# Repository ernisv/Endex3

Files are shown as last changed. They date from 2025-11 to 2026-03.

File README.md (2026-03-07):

# Project "Endex3"
Ender 3 Idex conversion

Prototype:

<p align="center">
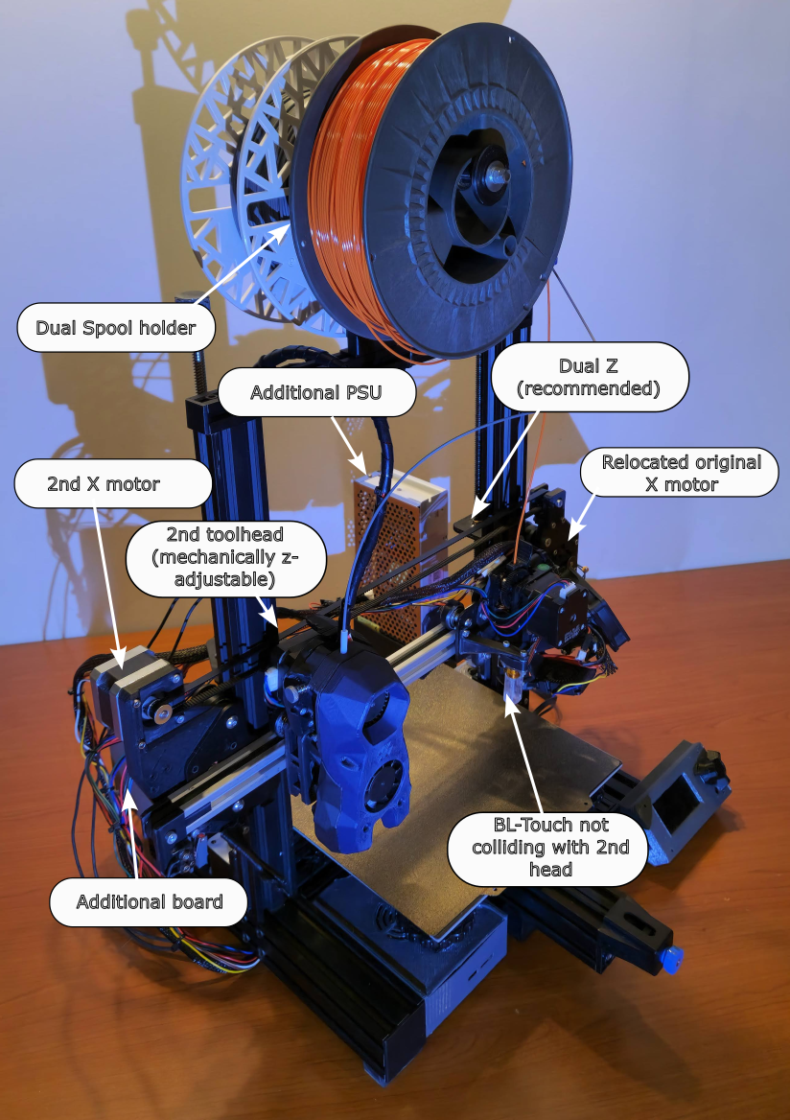
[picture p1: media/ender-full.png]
Conversion in reality

</p>

Idex in action:
[Idex in action](media/idex-in-action.mp4)

## Would like to get a support?
* Ask in platforms below
* Use Github issues
* Ask in [discord](https://discord.gg/aMRszwNQSe)

## Would like to support?
If you like the project or find it useful, you may support it here:
* https://buymeacoffee.com/ernisv
* https://patreon.com/ernisv

## Goals

* fully functional Idex
  * multimaterial printing without excessive filament/print time waste
  * copy mode
  * mirror mode
* no loss of printable area for at least one of the heads
* ooze prevention for idle nozzle
* controlled by Klipper firmware
* footprint width not to exceed 50cm
* reuse of commodity 3d printing parts of Ender3 era

## Additional hardware 

* NEMA17 stepper motor for new toolhead with wires
* GT2 6mm belt - about 90cm
* GT2 pulley for the motor
* GT2 idler
* 3 additional V-Wheels
* various M3 and M5 bolts (inner hex heads)
* M4 bolt for additional X GT2 idler
* 2 compression springs (~20nn) for M5 bolts on height adjustable toolhead mount
* microswitch for second X endstop
* 410mm 2020 extrusion for longer X gantry
* new toolhead - extruder with stepper, heating block, thermistor, hotend and part cooling fan, wires
* Klipper compatible control board to control:
  * 2 stepper motors - additional X motor, additional extruder
  * control new toolhead's heater
  * control new toolhead's part cooling fans
  * monitor new toolhead's temperature
* additional power needs  
  * can be small additional ~220W PSU that could power the heated bed
  * or complete 550W+ replacement for original PSU
  
## Conversion story
So before all that there was a Creality Ender3 V2, which was a first printer and during many years it morphed little by little to gain more speed, more flowrate, bed levelling, magnetic bed, Klipper.. and still was printing reliably enough to avoid being replaced by anothing more modern :)

But there was still a feature that it missed - multimaterial printing. And in 2025 - year when multimaterial became the norm with all multiplexing filament changers and even proper toolchangers coming, this became a matter of survival for the Ender3..

And the solution for that was one - Idex conversion. Idex is better than filament changers as produces less waste and switches materials much faster and even offers some interesting unique features that even proper toolchangers do not have - copy and mirror modes when single printer essentially is doing work for two :) 

So it started in CAD, trying to sqeeze additional axis belt, motors and toolhead while keeping bulky v-wheels system and most stock hardware.. 

After some time theoretically everything looked good in CAD.. did not work in practice though :)

First issues were random resets when bed heating and both toolheads were working simultaneously. 
In fact stock PSU now had to support 3 new stepper motors:
- dual X motor (one of previous mods), new extruder motor and new X motor,
- additional hotend heater,
- additional fans.
So it was solved by getting additional 24V PSU and it taking care of powering heated bed, so that all the rest could stay on original PSU.

At this point and quite a bit of calibrations and tuning, this amazing print was produced by both toolheads collaboratively.

<p align="center">
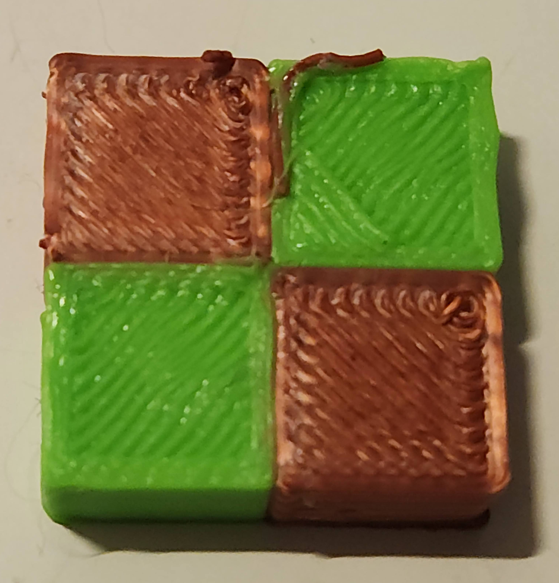
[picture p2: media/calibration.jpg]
Idex calibration done

</p>

It looked like a success.. but bigger prints still failed after some time - printheads were clogging. Especially the original Ender3 hotend. 
It was already modified previously - all metal heatbreak and Volcano nozzle for bigger flowrate, it even had bigger 60mm hotend fan in place of stock 3010 to solve the previous issues with heat creep. 
And this worked for single toolhead prints, when there was constant flow of filament being pushed through.

However now, when it needed to sit idle for minutes between extrusions - old issues came back.. so in the end to complete Idex conversion, stock hotend had to be replaced.

Checking the drawers yielded V6 hotend and direct drive Titan extruder. None of existing public designs for direct drive with hardware i had at hand did fit due to contraints of additional X belt and second toolhead, so it ment one - back to the CAD again..

And it worked out, but produced this monstrocity. This is not a suggestion to use the same for anyone wanting to do similar conversion by any means :) 

<p align="center">
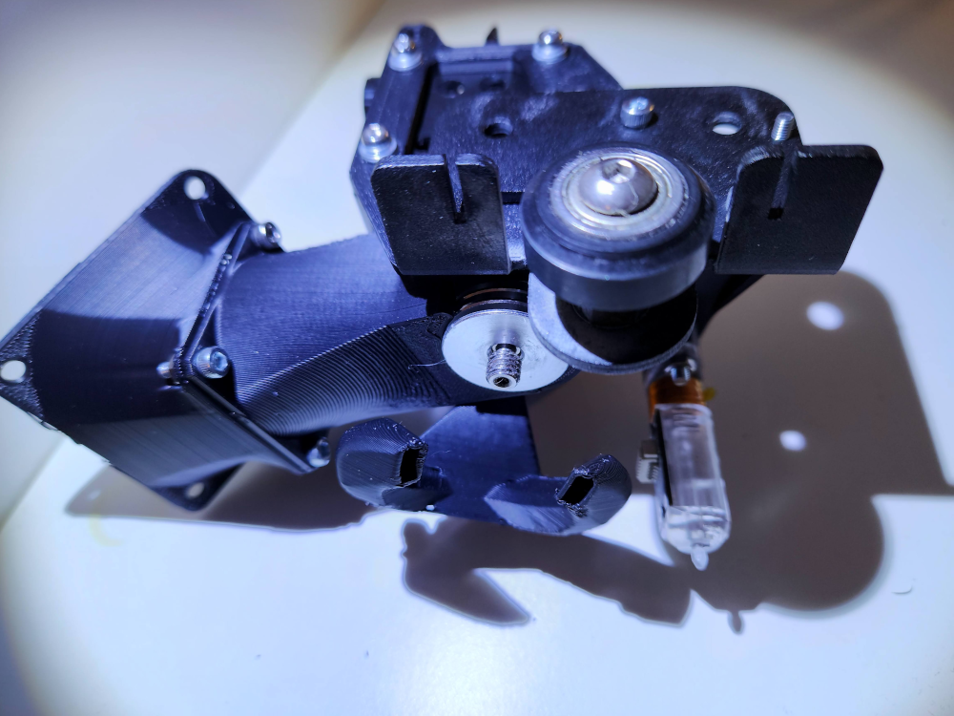
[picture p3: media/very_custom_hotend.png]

</p>

And finally it was working, evidence below !

<p align="center">
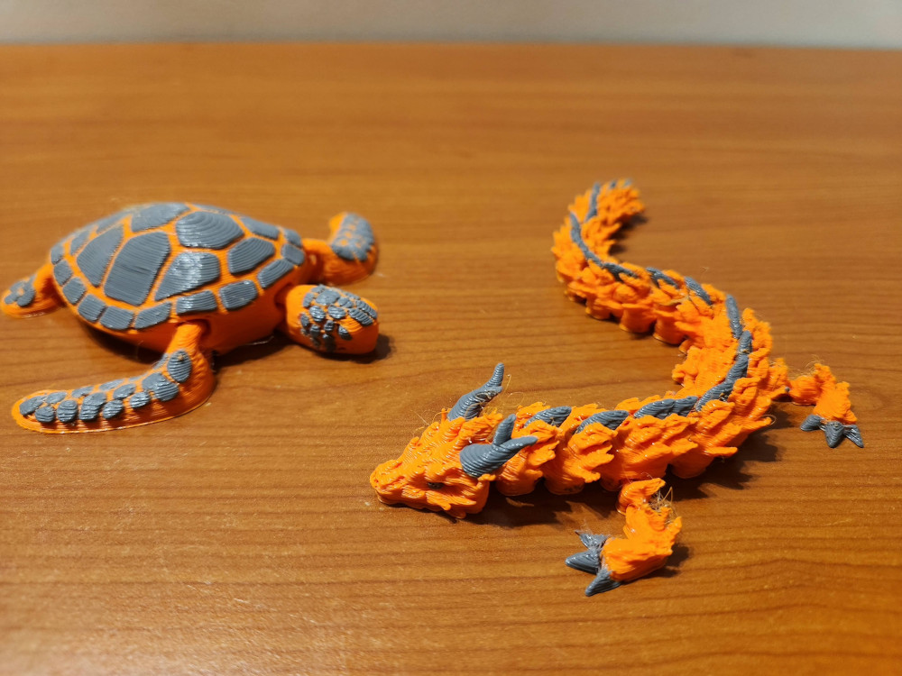
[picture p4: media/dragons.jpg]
Idex prints

</p>

What looked like a quick, relatively straightforward mod, took way more than expected - but now it's finished and working. It's shared here as there are not a lot of public designs leveraging mostly stock parts.
Also i'm sharing the same parts here:
* https://www.printables.com/@ErnestasVai_465342/models
* https://www.thingiverse.com/ernisv/designs

Now let's dive into each individual component/change to be able to create more Endexes.

Also if your drawers have different components - adaptations and variations of this conversion could be gathered here, please raise a Pull Request with suggested changes.

## Details / component changes
Changes to individual components are broken down below. If unsure about dimensions / assembly - step files and/or original [Onshape CAD](https://cad.onshape.com/documents/81a2e00ae9c5806eab5e1c54/w/5cac38db4e9fa7317548eab6/e/0372a484cd82c8e6febd21dc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) could be checked.

STLs from CAD are exported here: [STL](STL).

When "left" or "right" is mentioned, it's from perspective of looking at the printer from the front.

### X gantry
#### Longer 2020 extrusion
As stock x axis has space only for original head, putting another one on the same would significantly reduce the bed area accessible by any single head, so extension of this is necessary.
This is likely the most mechanically difficult part of the conversion as it needs replacement of stock extrusion and drilling correct holes at the same places as in old one.

The length of new 200 v-slot extrusion should be 410mm (could be reduced to around 400mm, but endstop mount will have to be mounted in some more compact way).

It is important to ensure that the left end (from perspective of looking at the printer from the front) of new extrusion is protruding 65mm from the end of original one, then original extrusion could be fixed together with the new one and used as a guide for drilling pilot holes.
To doublecheck - distance from the new extrusion left end to the first hole center should be 68mm.

<p align="center">
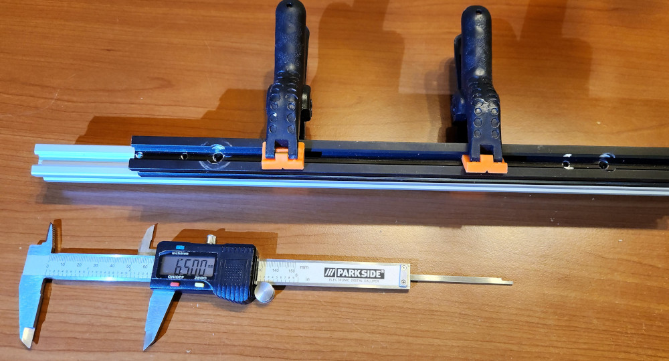
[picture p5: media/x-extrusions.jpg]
X Extrusions

</p>

*Note:* it needs to be v-slot extrusion, not t-slot, cause t-slot is not designed for v-wheels.

Once pilot holes are drilled - you will need to complete the drilling and tap the threads in M3 holes.

You will need:
* 3mm drill bit,
* 5.5mm drill bit,
* M3 tap,
* 11mm drill bit or dremel to clear space for M5 bolt heads from one side.

#### Original X belt / motor
With longer extrusion, original X motor placement is no longer an option. But moving motor further to the left would not allow to fit into 50cm width footprint.
So original X motor had to go to the right side onto newly designed mount where previously was a x belt tensioner.
Belt still goes inside the extrusion like before.

### Additional X belt
Now when original X motor was relocated to the right side, to keep weights balanced - new X motor should go to left side on new mount plate.
The required new GT2 6mm belt length is about 90cm.

#### X endstops
Left endstop is a microswitch having 2 holes for M3 with 10mm distance between them.
<p align="center">
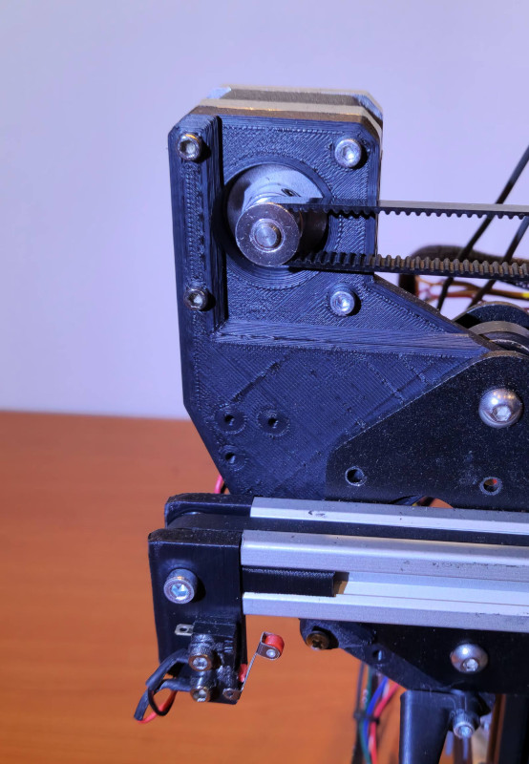
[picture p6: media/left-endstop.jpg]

</p>

Right one has a mount sliding into extrusion and bolting on original x endstop.
<p align="center">
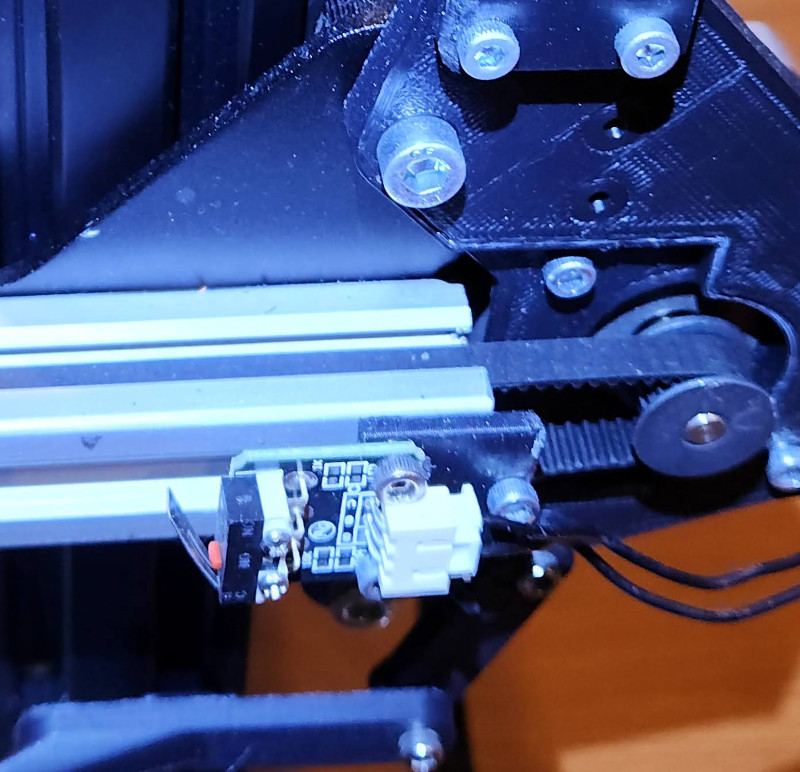
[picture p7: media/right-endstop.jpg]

</p>

#### Ooze prevention
Idling heads will ooze some filament even if slicer reduces idle temperatures - they won't drop immediately. To help with that, X gantry includes ooze blockers, that cover the nozzles when heads are in idle park positions.

They are slightly adjustable, printed in ABS and are supposed to have clamped strips of high temp silicone for the immediate contact area with the nozzles. Simplest way is to take heatblock silicone socks and cut out strips from them.

<p align="center">
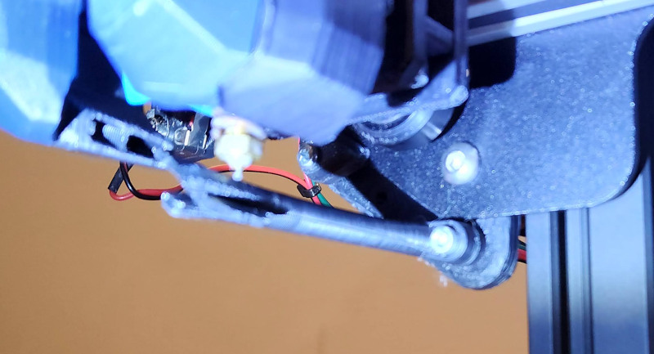
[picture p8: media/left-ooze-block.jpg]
Left ooze block

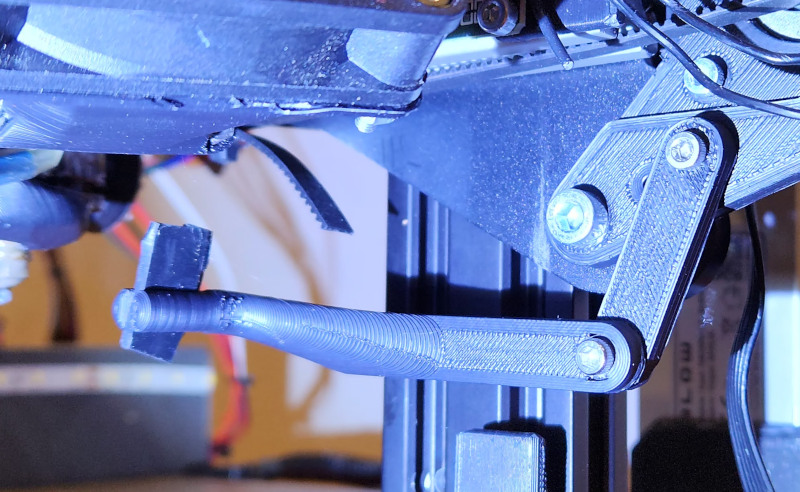
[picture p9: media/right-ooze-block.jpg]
Left ooze block

</p>

#### Dual Z
It's not strictly necessary, but highly recommended as weight of x gantry has increased.
This conversion has no particular solution included, but there are lots of publicly available options for Ender3 v2 dual Z axis.

#### Gantry levelling
With increased X gantry weight there are more possibilities for it to get out of alignment. If dual Z solution uses belt-synchronized Z sides, it may be less relevant, but still useful.

This conversion has two blocks of equal size on which X extrusion could be rested until a touch (manually, with heads out of bed area in park positions).
Right block can remain attached permanently, but left one blocks X head movement when attached, so it is a clip-on to be attached only during alignment.
<p align="center">
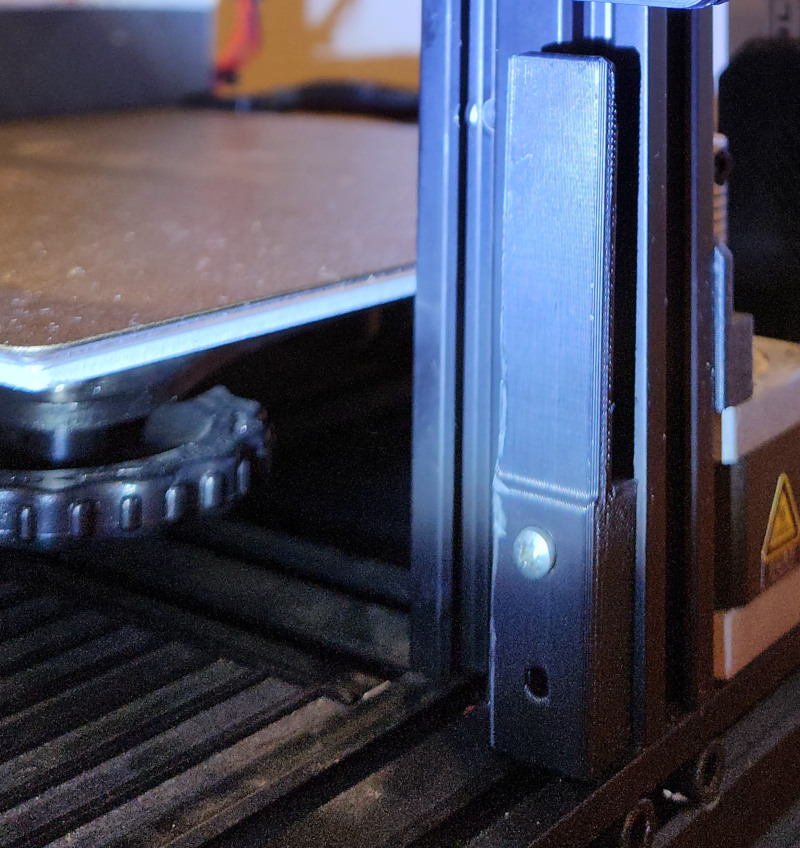
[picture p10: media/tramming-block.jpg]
Left ooze block

</p>

### 2nd toolhead
#### Stealthburner
2nd toolhead has limited access across X axis, so the narrower it is - the less limitation. 
And Voron's Stealthburner looked like a quite compact option with regard to X-footprint.

Also it's a popular toolhead with lots of mods, which helped me to use the components i had available.
I had pancake NEMA17 motor, V6 heatsink with Volcano nozzle, so i used these mods to make use of them.

* [V6+Volcano mod](https://www.printables.com/model/561529-voron-stealthburner-v6volcano-toolhead-extension-m)
* [NEMA17 pancake mod](https://www.printables.com/model/454292-voron-stealthburner-clockwork2-extruder-nema17-v1)
  * *note:* use idler from the step files, as STL has some older incompatible part (see comments)

#### Mechanical Z adjustments
Nozzles of both Idex heads should be aligned vertically in relation to each other with quite a high precision (to be at least a fractions of of a layer's hight).

While for dual-material printing maybe it could be adjusted by software z-offsets, for copy/mirror mode especially - they need to be physically aligned.
Because of that a mount with mechanically adjustable height was designed.

<p align="center">
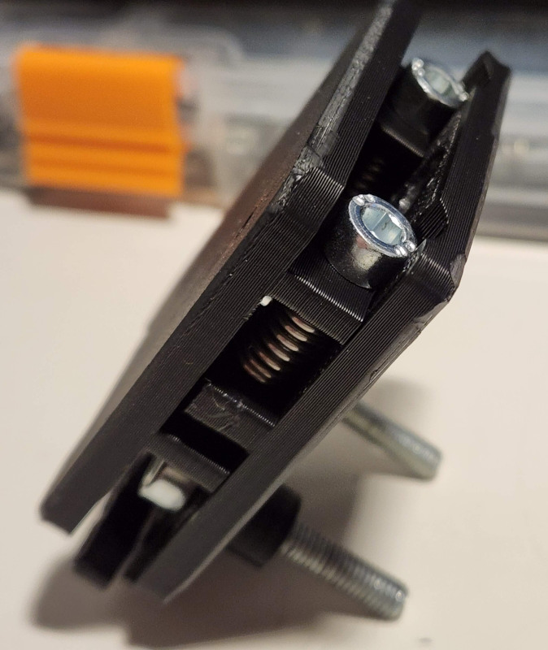
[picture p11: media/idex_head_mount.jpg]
Idex adjustable head mount

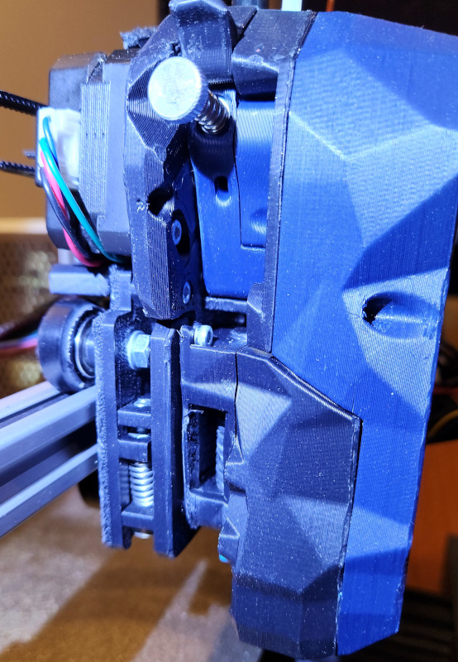
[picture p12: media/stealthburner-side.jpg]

</p>

Here some springs were used together with M5 adjustability bolts, you need to adjust both bolts equally to avoid skew.

The alignment process i used:
* home the printer, clear the heightmap
* via Klipper web UI move the original nozzle somewhere near the middlge of the bed and lower to minimal distance from bed like in "paper test" (paper sheet just lightly gripped between nozzle and bed surface)
* raise Z, change the active head to secondary
* near the same bed point carefully try to lower the nozzle to the same z position original nozzle hand
  * if paper grips earlier or later than first nozzle - raise the Z, adjust the adjustment screws and recheck 

### Original toolhead
Stock bowden toolhead should work fine with this conversion. My prototype used volcano nozzles, which are 8.5mm longer on both toolheads, but basically what's required is that both tools would have nozzles at roughly the same height, that would be within adjutability range of Idex head mount. 
So if stock head and nozzle is used - stealthburner should also use nozzle of similar height to stock nozzle, not Volcano height.

#### Bed probe
Also most likely you already use some kind of bed probe, prototype printer used Bltouch. Common probe mounts might occupy more space than necessary on the side of toolhead, which would limit how close both heads could come together. So this conversion includes Bltouch mount that moves it furter forward, but occupying less space along X axis.

<p align="center">
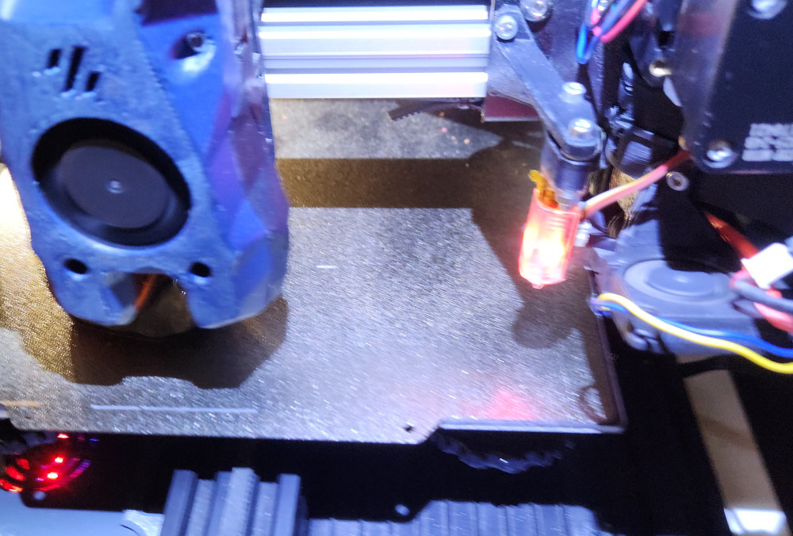
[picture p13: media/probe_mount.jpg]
Bed probe mount

</p>

#### Suitable alternatives
Prototype needed some custom adjustments, because it used direct drive conversion with full size NEMA17 motor and most direct drive mods with such motor did not clear space above the X extrusion to clear the belts and allow additional travel to the right. 

But that does not mean there wouldn't be suitable direct drive mods with more compact components that are compatible.

So what needs to be considered when choosing direct drive mod:
* clearance for the additional belts above X extrusion,
* clearance of additional travel to the right - it should not hit Y extrusion,
* distance from the left of the head - isn't it limiting how close both heads could come together,
* the endstop from the right.

### Second control board
Prototype printer had already replaced stock board to SKR Mini E3, however as this and most usual replacement boards would not support additional 2 stepper motors, heater, thermistor and fan - second board would be needed.
I used stock Ender3 board for that.

In general you just need to connect and setup 2 boards to the device running Klipper (usually SBC like Raspberry Pi or regular linux PC).

### Additional PSU
As it turns out stock PSU capacity might be not enough to power all additional hardware - it either needs to be replaced by more powerful one - 550W should be enough.

Or as a more budget option - add a smaller additional PSU to just power the heated bed, which would take quite a big portion of load from original PSU.
Moreover there is a place to mount PSU like original Ender3's did - on the right/back.

Mounting options are also plenty, it depends on exact PSU you have. The mount included in conversion is for "Blow 24V PSU" i've got (still running.. still not blown!).

The stock Ender3v2 bed should take around 220W.

Klipper's config setting `max_power` could also be used to try limiting power consumption.

How i connected additional PSU to work only as dedicated PSU for heated bed:
* New PSU ground / earth <--> Old PSU ground / earth
* New PSU -24V <--> Old PSU -24V
* New PSU +24V <--> Bed +
* Board Bed - <--> Bed -
* Board Bed + <--> *Unconnected!*

This is done so, because MOSFET on the board controls connection to the -, while Bed+ provides constant +24V from PSU.

<p align="center">
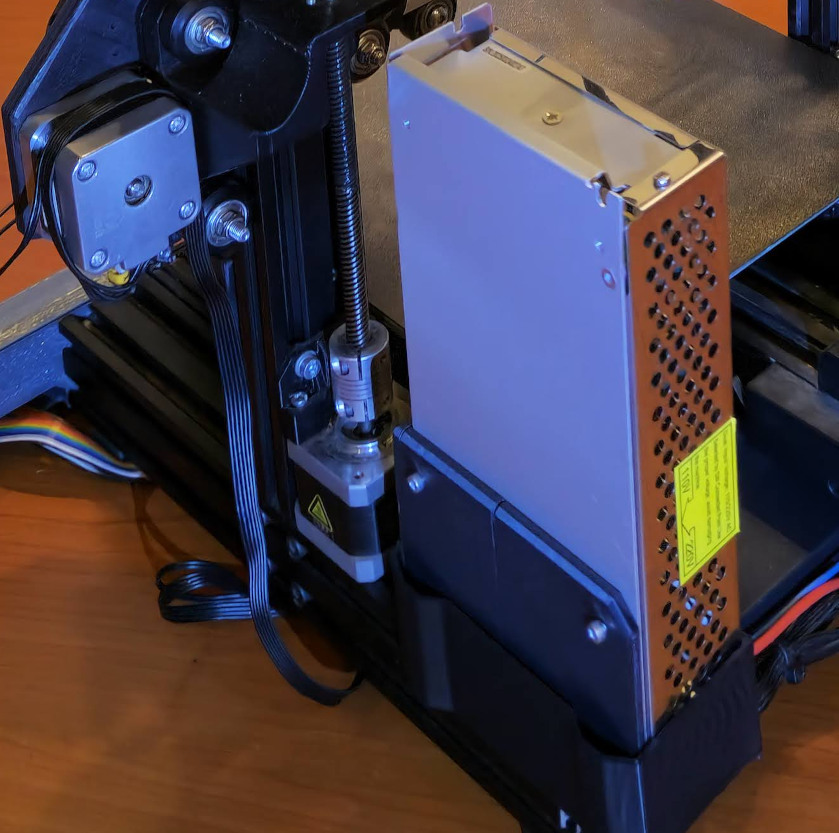
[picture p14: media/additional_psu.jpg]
Additional PSU

</p>

### Klipper configs

[Klipper configs](KlipperConfigs) directory contains example of Klipper config files used in the prototype. 
It won't be drop-in config, but rather an example to base on, so that assumes basic Klipper knowledge.

### Printing the parts
I tried to design parts to not require supports, so most parts can be printed without them.
Although i printed all the parts in ABS - i did so because that printer is usually printing in an enclosure, where it could get pretty hot.
But if it's not the case - ABS would only be recommended for parts closer to hotends, like fan ducts, heatsink mounts, also ooze blocks.
Other parts should work fine printed with PETG/PLA. 

## Contributing mods / improvements
If you make an improvement or adaptation - let others know by raising a PR! 
We'll merge it into this repository and maybe this could become a modular and flexible project.

If it's not a change to existing parts, but alternative/adaptation, it could go to separate directory with small individual description, then we could create easily searchable list of mods.

List of improvements currently needing work can be found in [TODO.txt](TODO.txt).

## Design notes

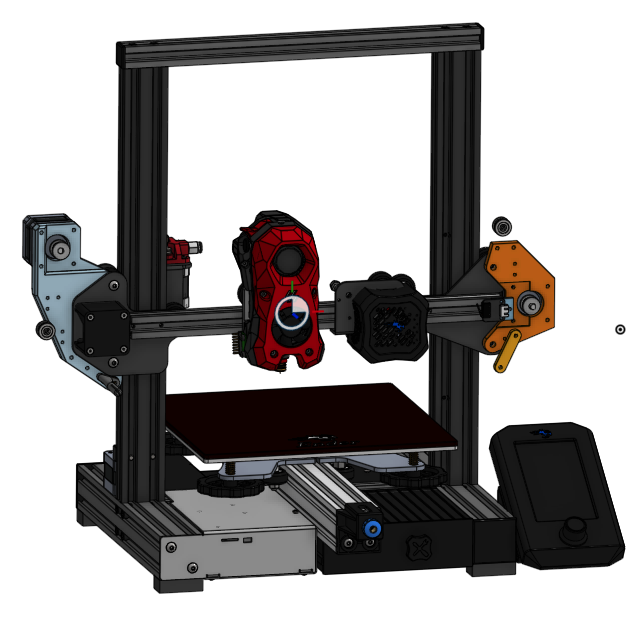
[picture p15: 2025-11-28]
media/ender-cad.png

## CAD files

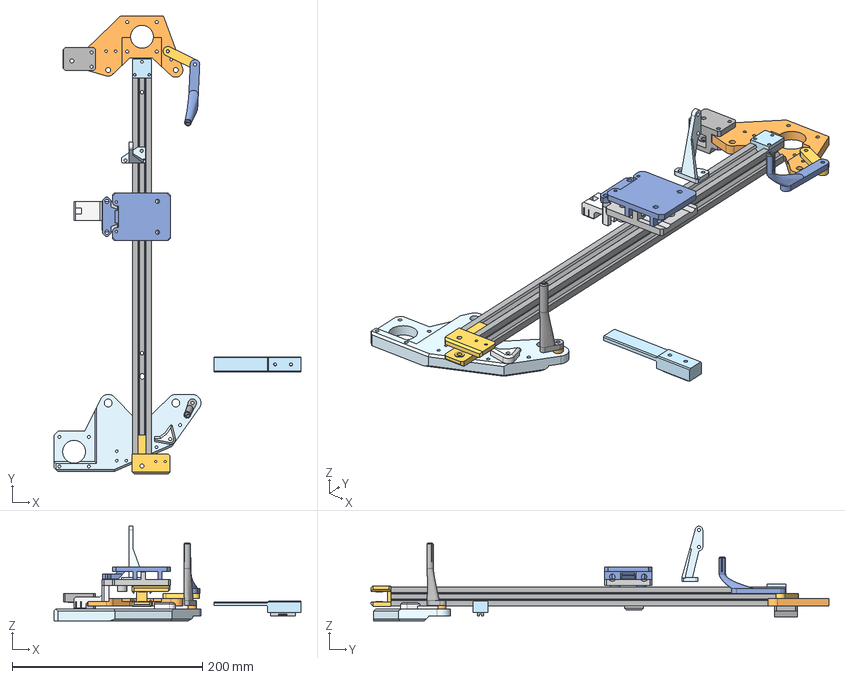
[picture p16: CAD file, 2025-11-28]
STEP/XGantry.step
259.5 x 481.3 x 99.5 mm

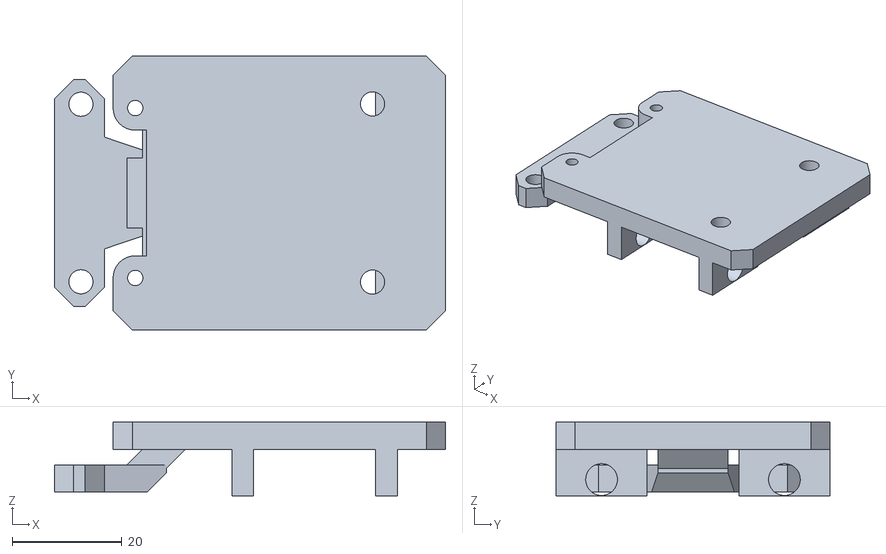
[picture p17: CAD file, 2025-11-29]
STL/XGantry - StealthburnerBracket.stl
71.3 x 50.0 x 13.5

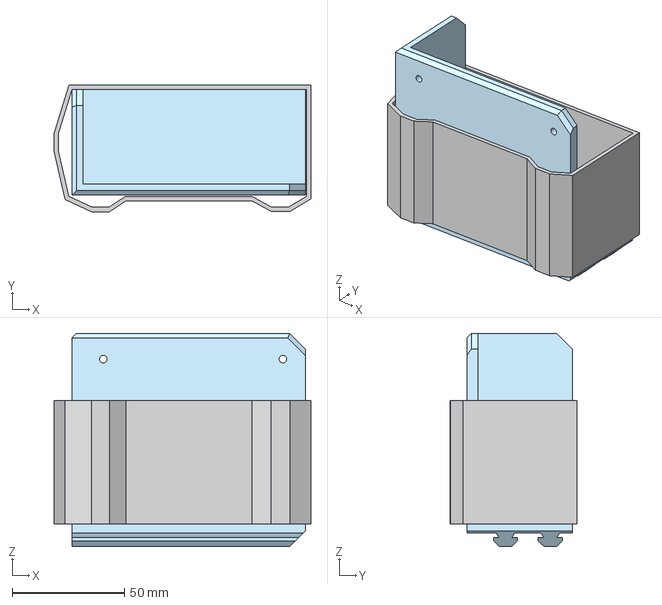
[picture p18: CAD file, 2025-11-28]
STEP/Misc Parts - PSU Mount.step
114.5 x 56.4 x 95.0 mm

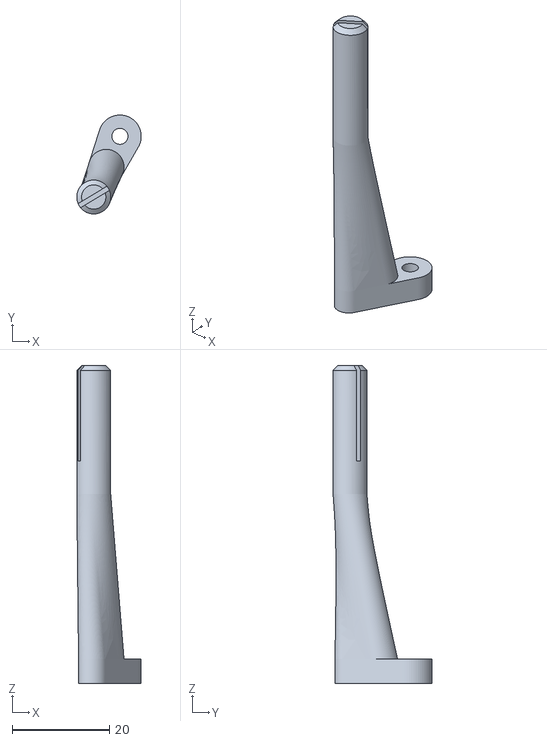
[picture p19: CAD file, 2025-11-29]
STL/XGantry - LeftOozeBlock.stl
13.3 x 20.4 x 65.5

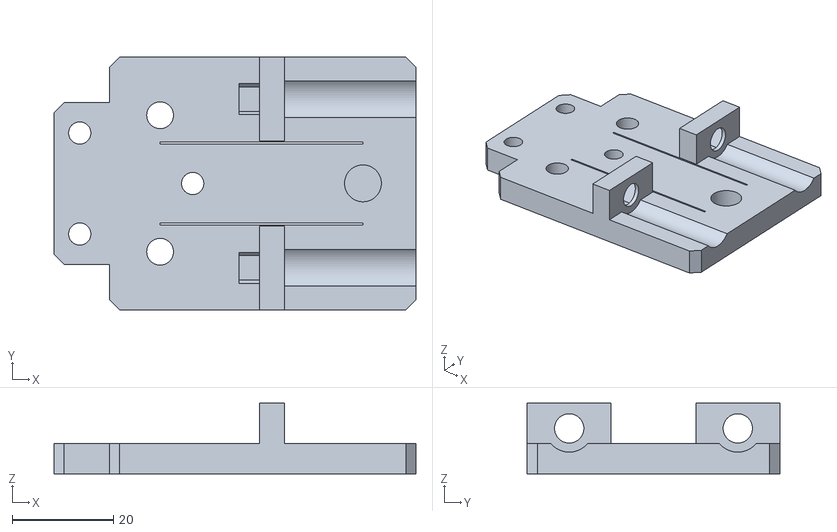
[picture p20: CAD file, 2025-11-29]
STL/XGantry - StealthburnerCarriage.stl
71.6 x 50.0 x 14.0

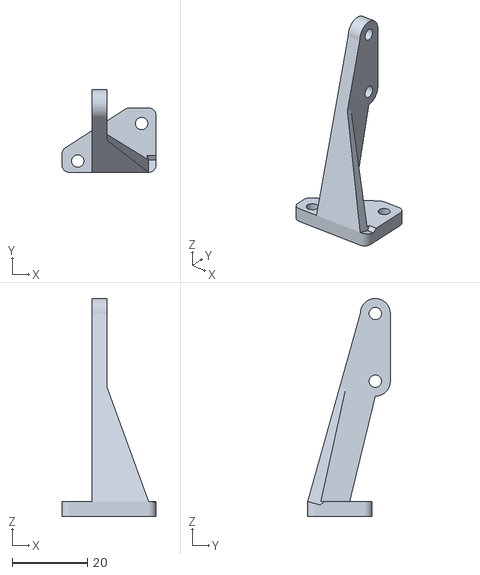
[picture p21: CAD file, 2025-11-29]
STL/XGantry - BLTouchMount.stl
25.1 x 22.0 x 58.0

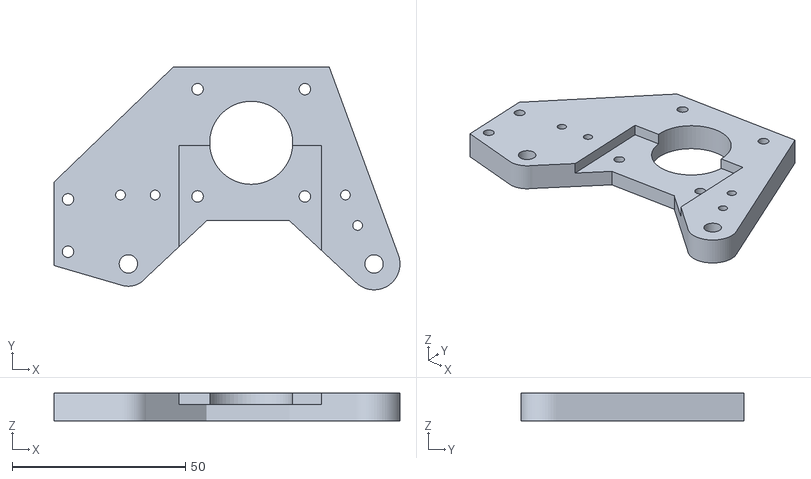
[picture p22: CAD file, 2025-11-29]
STL/XGantry - RightXMotorMount.stl
100.0 x 64.4 x 8.00

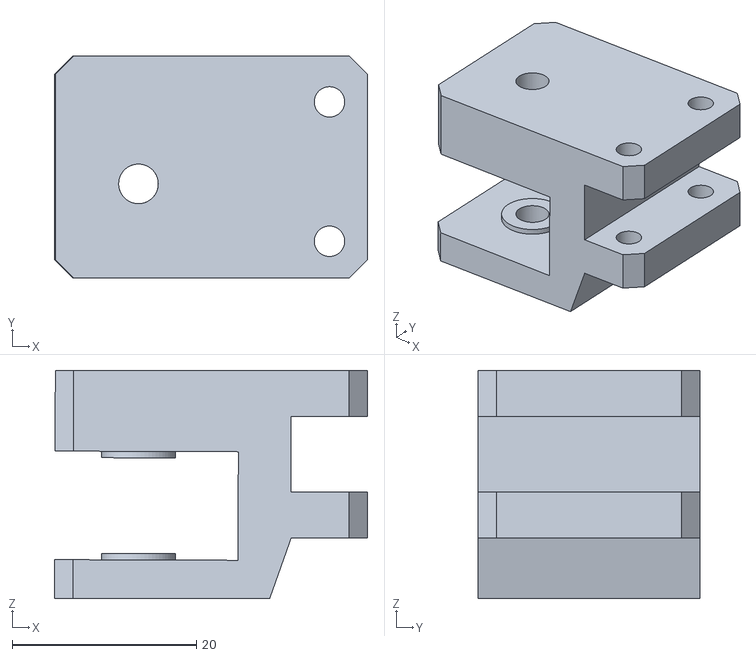
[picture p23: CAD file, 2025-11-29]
STL/XGantry - RightXIdlerMount.stl
34.0 x 24.1 x 24.8

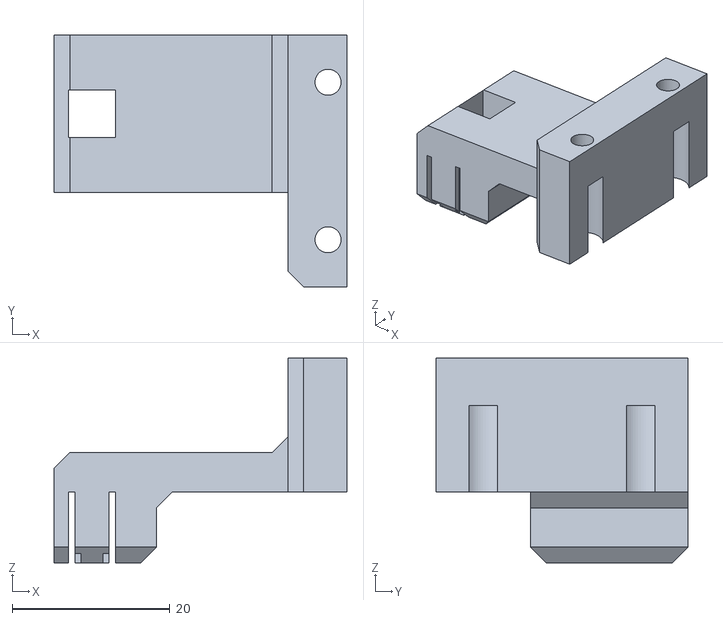
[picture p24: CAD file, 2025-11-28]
STL/XGantry - GantryBeltBracket.stl
37.2 x 32.0 x 26.0

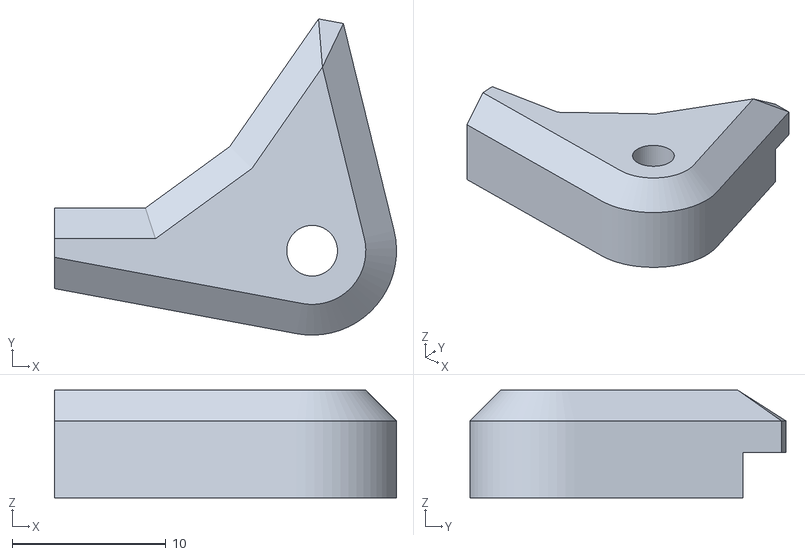
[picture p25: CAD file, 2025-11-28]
STL/XGantry - LeftXMotorMountBracket.stl
22.3 x 20.6 x 7.00

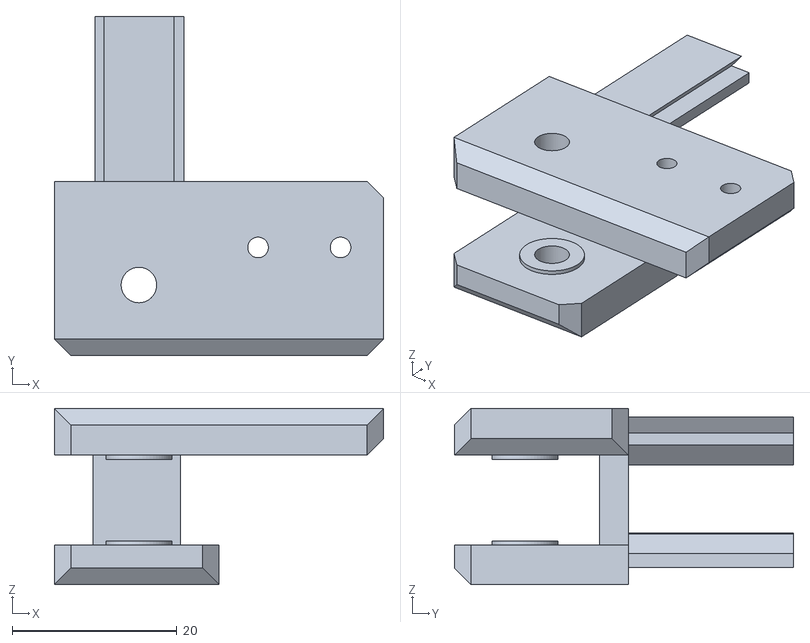
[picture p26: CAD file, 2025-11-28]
STL/XGantry - LeftEndstopAndIdler.stl
39.9 x 41.1 x 21.4

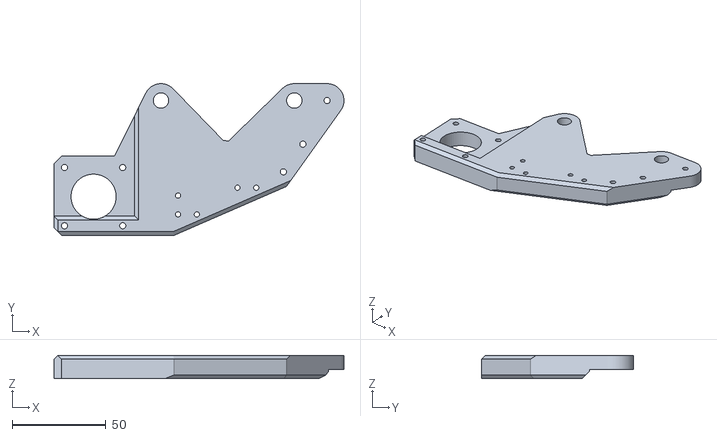
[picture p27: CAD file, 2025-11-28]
STL/XGantry - LeftXMotorMount.stl
154.4 x 80.8 x 12.5

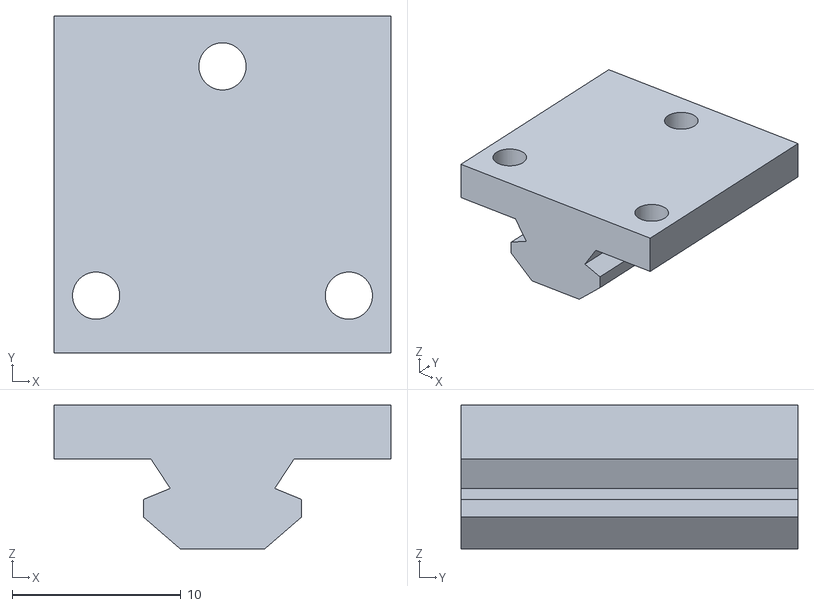
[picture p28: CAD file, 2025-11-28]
STL/XGantry - RightEndstop.stl
20.0 x 20.0 x 8.54

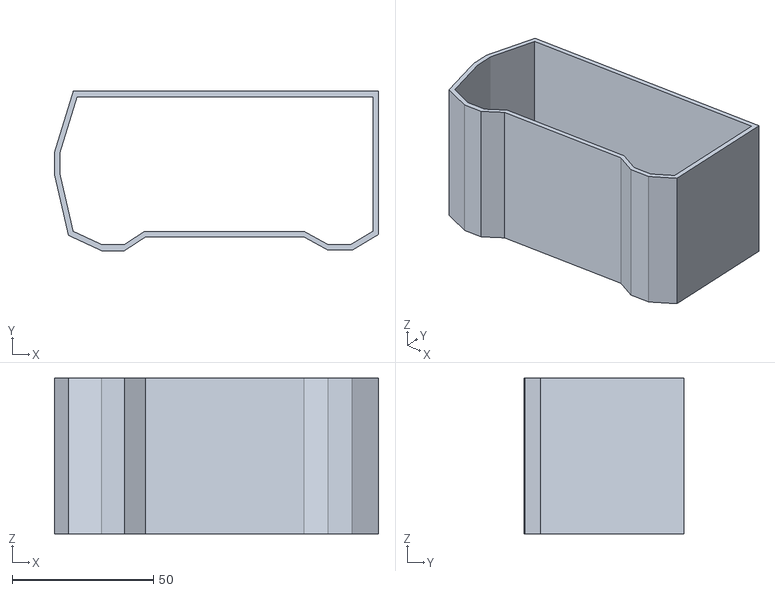
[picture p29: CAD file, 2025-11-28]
STL/Misc Parts - PsuCover.stl
114.5 x 56.4 x 55.0

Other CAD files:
STL/XGantry - RightOozeBlock2.stl
STL/XGantry - RightOozeBlock1.stl
STL/XGantry - LeftOozeBlockSpacer.stl
STL/XGantry - TrammingBlock.stl
STL/Misc Parts - PsuMount.stl
STL/XGantry - TrammingBlockClip.stl
STL/XGantry - XVWheelSpacer.stl

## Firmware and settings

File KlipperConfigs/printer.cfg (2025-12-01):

[gcode_macro _CLIENT_VARIABLE]
variable_use_custom_pos   : True ; use custom park coordinates for x,y [True/False]
variable_custom_park_x    : 100.0   ; custom x position; value must be within your defined min and max of X
variable_custom_park_y    : 190.0   ; custom y position; value must be within your defined min and max of Y
variable_custom_park_dz   : 10.0   ; custom dz value; the value in mm to lift the nozzle when move to park position
variable_retract          : 1.0   ; the value to retract while PAUSE
variable_cancel_retract   : 5.0   ; the value to retract while CANCEL_PRINT
variable_speed_retract    : 35.0  ; retract speed in mm/s
variable_unretract        : 1.0   ; the value to unretract while RESUME
variable_speed_unretract  : 35.0  ; unretract speed in mm/s
variable_speed_hop        : 15.0  ; z move speed in mm/s
variable_speed_move       : 100.0 ; move speed in mm/s
variable_park_at_cancel   : False ; allow to move the toolhead to park while execute CANCEL_PRINT [True/False]
variable_park_at_cancel_x : None  ; different park position during CANCEL_PRINT [None/Position as Float]; park_at_cancel must be True
variable_park_at_cancel_y : None  ; different park position during CANCEL_PRINT [None/Position as Float]; park_at_cancel must be True
# !!! Caution [firmware_retraction] must be defined in the printer.cfg if you set use_fw_retract: True !!!
variable_use_fw_retract   : False ; use fw_retraction instead of the manual version [True/False]
variable_idle_timeout     : 0     ; time in sec until idle_timeout kicks in. Value 0 means that no value will be set or restored
variable_runout_sensor    : ""    ; If a sensor is defined, it will be used to cancel the execution of RESUME in case no filament is detected.
#                                   Specify the config name of the runout sensor e.g "filament_switch_sensor runout". Hint use the same as in your printer.cfg
# !!! Custom macros, please use with care and review the section of the corresponding macro.
# These macros are for simple operations like setting a status LED. Please make sure your macro does not interfere with the basic macro functions.
# Only  single line commands are supported, please create a macro if you need more than one command.
variable_user_pause_macro : ""    ; Everything inside the "" will be executed after the klipper base pause (PAUSE_BASE) function
variable_user_resume_macro: ""    ; Everything inside the "" will be executed before the klipper base resume (RESUME_BASE) function
variable_user_cancel_macro: ""    ; Everything inside the "" will be executed before the klipper base cancel (CANCEL_PRINT_BASE) function
gcode:

[include mainsail.cfg]
[include idex.cfg]
[include macros.cfg]

# enable when RPi Pico with accelerometer is connected for resonance measurement
#[include accelerometer.cfg]


[exclude_object]

# MKS Robin E3 V1.1
[mcu]
serial: /dev/serial/by-path/pci-0000:06:00.4-usbv2-0:2.4:1.0-port0
#serial: /dev/ttyUSB1
#serial: /dev/serial/by-id/usb-1a86_USB_Serial-if00-port0
restart_method: command

# Stock Ender3v2 board
[mcu mcu2]
serial: /dev/serial/by-path/pci-0000:06:00.4-usbv2-0:2.3:1.0-port0
#serial: /dev/ttyUSB0
restart_method: command


[virtual_sdcard]
path: /home/ernis/printer_data/gcodes
on_error_gcode: CANCEL_PRINT

[tmc2209 stepper_x]
uart_pin: PC7
run_current: 0.600
hold_current: 0.400
stealthchop_threshold: 999999

[stepper_x]
step_pin: PC0
dir_pin: PB2
enable_pin: !PC13
microsteps: 16
rotation_distance: 40
endstop_pin: ^PA12
position_endstop: 322
position_min: 70
position_max: 322
homing_positive_dir: true
homing_speed: 70

[tmc2209 stepper_y]
uart_pin: PD2
run_current: 0.650
hold_current: 0.400
stealthchop_threshold: 999999

[stepper_y]
step_pin: PC2
dir_pin: PB9
enable_pin: !PB12
microsteps: 16
rotation_distance: 40
endstop_pin: ^PA11
position_endstop: 0
position_max: 230
homing_speed: 70

[tmc2209 stepper_z]
uart_pin: PC12
run_current: 0.650
hold_current: 0.450
stealthchop_threshold: 999999

[stepper_z]
step_pin: PC14
dir_pin: !PC15
enable_pin: !PB8
microsteps: 16
rotation_distance: 8
endstop_pin: probe:z_virtual_endstop
position_max: 250
position_min: -1

[exclude_object]

[input_shaper]
shaper_freq_x: 39
shaper_freq_y: 39
shaper_type: 2hump_ei

[bltouch]
sensor_pin: ^PB1
control_pin: PA3
x_offset: -30
y_offset: -28
z_offset: 2.1
pin_up_reports_not_triggered: False

[bed_mesh]
speed: 120
horizontal_move_z: 10
mesh_min: 127, 40
mesh_max: 291, 200
probe_count: 4, 4
fade_start: 1
fade_end: 10
fade_target: 0

[safe_z_home]
home_xy_position: 230, 125 # Change coordinates to the center of your print bed
speed: 50
z_hop: 10                 # Move up 10mm
z_hop_speed: 5

[tmc2209 extruder]
uart_pin: PC11
run_current: 0.700
hold_current: 0.350
stealthchop_threshold: 999999

[extruder]
step_pin: PB4
dir_pin: PB3
enable_pin: !PB5
max_extrude_only_distance: 100.0
microsteps: 16
#rotation_distance: 32.35
rotation_distance: 7.711
nozzle_diameter: 0.600
filament_diameter: 1.750
heater_pin: PC9
sensor_type: EPCOS 100K B57560G104F
sensor_pin: PA0
#control: pid
#pid_Kp: 27.924
#pid_Ki: 2.024
#pid_Kd: 96.339
min_temp: -120
max_temp: 250
pressure_advance: 0.055
pressure_advance_smooth_time: 0.050
min_extrude_temp: 139


[heater_bed]
heater_pin: PC8
sensor_pin: PA1
sensor_type: EPCOS 100K B57560G104F
#control: pid
max_power: 0.85   # limit power usage a bit
#pid_Kp: 73.594
#pid_Ki: 1.553
#pid_Kd: 872.087
min_temp: -120
max_temp: 110

[fan]
pin: PA8


[led light]
cycle_time: 0.010
white_pin: mcu2:PA2

[filament_switch_sensor filament_sensor]
pause_on_runout: True            # Automatically PAUSE the print
runout_gcode: PAUSE              # What to run if filament runs out
insert_gcode: RESUME             # Auto-resume when filament inserted

switch_pin: ^!PB10                  # "^" = enable pull-up (required for open switch)


[printer]
kinematics: cartesian
max_velocity: 300
max_accel: 3500
max_z_velocity: 5
max_z_accel: 100

[delayed_gcode bed_mesh_init]
initial_duration: .01
gcode:
  BED_MESH_PROFILE LOAD=default

# EXP1 / EXP2 (display) pins
[board_pins]
aliases:
    # EXP1 header
    EXP1_1=PC1, EXP1_3=PA4, EXP1_5=PA6, EXP1_7=PC4, EXP1_9=<GND>,
    EXP1_2=PC3, EXP1_4=PA5, EXP1_6=PA7, EXP1_8=PC5, EXP1_10=<5V>,
    # EXP2 header
    EXP2_1=PB14, EXP2_3=PB11, EXP2_5=PB0,  EXP2_7=PC10,  EXP2_9=<GND>,
    EXP2_2=PB13, EXP2_4=PA15, EXP2_6=PB15, EXP2_8=<RST>, EXP2_10=<NC>,
    
    # CR_EXP3 header - additional header dedicated to Creality Ender 3/5 stock screens
    CR_EXP3_10=<5V>, CR_EXP3_8=PA4, CR_EXP3_6=PA6, CR_EXP3_4=<RST>, CR_EXP3_2=PC3,
    CR_EXP3_9=<GND>, CR_EXP3_7=PA5, CR_EXP3_5=PB0, CR_EXP3_3=PB11,  CR_EXP3_1=PC1

# Makerbase MKS MINI12864 V3 
[display]
lcd_type: uc1701
cs_pin: EXP1_3
a0_pin: EXP1_4
rst_pin: EXP1_5
contrast: 63
encoder_pins: ^EXP2_5, ^EXP2_3
click_pin: ^!EXP1_2
## Some micro-controller boards may require an spi bus to be specified:
#spi_bus: spi
## Alternatively, some micro-controller boards may work with software spi:
spi_software_miso_pin: EXP2_1
spi_software_mosi_pin: EXP2_6
spi_software_sclk_pin: EXP2_2

[output_pin beeper]
pin: EXP1_1

[neopixel mks_mini12864]
pin: EXP1_6
chain_count: 3
color_order: RGB
initial_RED: 0.5
initial_GREEN: 1.0
initial_BLUE: 0.5

#*# <---------------------- SAVE_CONFIG ---------------------->
#*# DO NOT EDIT THIS BLOCK OR BELOW. The contents are auto-generated.
#*#
#*# [bed_mesh default]
#*# version = 1
#*# points =
#*# 	  -0.015000, -0.070000, -0.115000, -0.095000
#*# 	  -0.042500, -0.045000, -0.022500, 0.000000
#*# 	  0.045000, -0.040000, 0.032500, 0.130000
#*# 	  0.080000, 0.075000, 0.100000, 0.125000
#*# x_count = 4
#*# y_count = 4
#*# mesh_x_pps = 2
#*# mesh_y_pps = 2
#*# algo = lagrange
#*# tension = 0.2
#*# min_x = 127.0
#*# max_x = 290.98
#*# min_y = 40.0
#*# max_y = 199.99
#*#
#*# [heater_bed]
#*# control = pid
#*# pid_kp = 60.034
#*# pid_ki = 1.308
#*# pid_kd = 688.890
#*#
#*# [extruder]
#*# control = pid
#*# pid_kp = 26.033
#*# pid_ki = 1.736
#*# pid_kd = 97.624

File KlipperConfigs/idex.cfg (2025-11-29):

# Definition for the secondary carriage and extruder1
[dual_carriage]
axis: x
step_pin: mcu2:PB6
dir_pin: !mcu2:PB5
enable_pin: !mcu2:PC3
microsteps: 16
rotation_distance: 32  # depends on motor pulley size - doublecheck before use
endstop_pin: !mcu2:PA5
position_endstop: 0
position_min: 0
position_max: 240
homing_positive_dir: false
homing_speed: 70
# A minimum distance between the carriages to enforce
safe_distance: 82


[fan_generic idex_fan]
pin: mcu2:PA0
max_power: 1.0
kick_start_time: 0.2
off_below: 0.1
hardware_pwm: True
cycle_time: 0.010

[gcode_macro RESET_TOOLS]
gcode:
    SET_DUAL_CARRIAGE CARRIAGE=0 MODE=PRIMARY
    SET_GCODE_OFFSET X=0 Y=0
    ACTIVATE_EXTRUDER EXTRUDER=extruder
    SYNC_EXTRUDER_MOTION EXTRUDER=extruder1 MOTION_QUEUE=extruder1

# controlling both hotends part cooling fan's simultaneously
[gcode_macro M106]
rename_existing: M106.1
gcode:
    {% set s = params.S|default(255)|float %}
    {% set speed = s / 255 %}
    M106.1 S{params.S}
    SET_FAN_SPEED FAN=idex_fan SPEED={speed}

[gcode_macro M107]
rename_existing: M107.1
gcode:
    M107.1
    SET_FAN_SPEED FAN=idex_fan SPEED=0

[extruder1]
step_pin: mcu2:PC2
dir_pin: mcu2:PB9
enable_pin: !mcu2:PC3
microsteps: 16
max_extrude_only_distance: 100.0
rotation_distance: 7.710
nozzle_diameter: 0.600
filament_diameter: 1.750
heater_pin: mcu2:PA1
sensor_type: EPCOS 100K B57560G104F
sensor_pin: mcu2:PC5
control: pid
pid_Kp: 26.952
pid_Ki: 1.711
pid_Kd: 106.126
min_temp: -30
max_temp: 250
pressure_advance: 0.04
min_extrude_temp: 139

# Helper script to park the carriage (called from T0 and T1 macros)
[gcode_macro PARK_extruder]
gcode:
    SAVE_GCODE_STATE NAME=park0
    SET_DUAL_CARRIAGE CARRIAGE=0
    G91
    G1 Z2 F3600
    G90
    G1 X321 F10800
    G91
    G1 Z-2 F3600
    RESTORE_GCODE_STATE NAME=park0

[gcode_macro PARK_extruder1]
gcode:
    SAVE_GCODE_STATE NAME=park1
    SET_DUAL_CARRIAGE CARRIAGE=1
    G91
    G1 Z2 F3600
    G90
    G1 X1 F10800
    G91
    G1 Z-2 F3600
    RESTORE_GCODE_STATE NAME=park1

# Activate the primary extruder
[gcode_macro T0]
gcode:
    PARK_{printer.toolhead.extruder}
    ACTIVATE_EXTRUDER EXTRUDER=extruder
    SET_DUAL_CARRIAGE CARRIAGE=0
    SET_GCODE_OFFSET X=0 Y=0
    SET_INPUT_SHAPER SHAPER_FREQ_X=39 SHAPER_FREQ_Y=39 SHAPER_TYPE=2hump_ei

[gcode_macro T1]
gcode:
    PARK_{printer.toolhead.extruder}
    ACTIVATE_EXTRUDER EXTRUDER=extruder1
    SET_DUAL_CARRIAGE CARRIAGE=1
    SET_GCODE_OFFSET X=1.55 Y=14.8
    SET_INPUT_SHAPER SHAPER_FREQ_X=52.2 SHAPER_FREQ_Y=39 SHAPER_TYPE=2hump_ei


# A helper script to activate copy mode
[gcode_macro ACTIVATE_COPY_MODE]
gcode:
    SET_DUAL_CARRIAGE CARRIAGE=0 MODE=PRIMARY
    G1 X100 F10800
    ACTIVATE_EXTRUDER EXTRUDER=extruder
    SET_DUAL_CARRIAGE CARRIAGE=1 MODE=PRIMARY
    G1 X0 F10800
    SET_DUAL_CARRIAGE CARRIAGE=1 MODE=COPY
    SYNC_EXTRUDER_MOTION EXTRUDER=extruder1 MOTION_QUEUE=extruder

# A helper script to activate mirror mode
[gcode_macro ACTIVATE_MIRROR_MODE]
gcode:
    SET_DUAL_CARRIAGE CARRIAGE=0 MODE=PRIMARY
    G1 X310 F10800
    ACTIVATE_EXTRUDER EXTRUDER=extruder
    SET_DUAL_CARRIAGE CARRIAGE=1 MODE=PRIMARY
    G1 X80 F10800
    SET_DUAL_CARRIAGE CARRIAGE=1 MODE=MIRROR
    SYNC_EXTRUDER_MOTION EXTRUDER=extruder1 MOTION_QUEUE=extruder

[gcode_macro PRINT_END]
#rename_existing: PRINT_END_BASE
gcode:
    RESET_TOOLS
    # --- call original PRINT_END actions ---
#    PRINT_END_BASE

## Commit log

2025-12-01 Update measurement for new extrusion hole distance
2025-12-01 Add filament switch sensor to printer configuration
    Added filament switch sensor configuration for automatic pause and resume.
    [printer.cfg]
